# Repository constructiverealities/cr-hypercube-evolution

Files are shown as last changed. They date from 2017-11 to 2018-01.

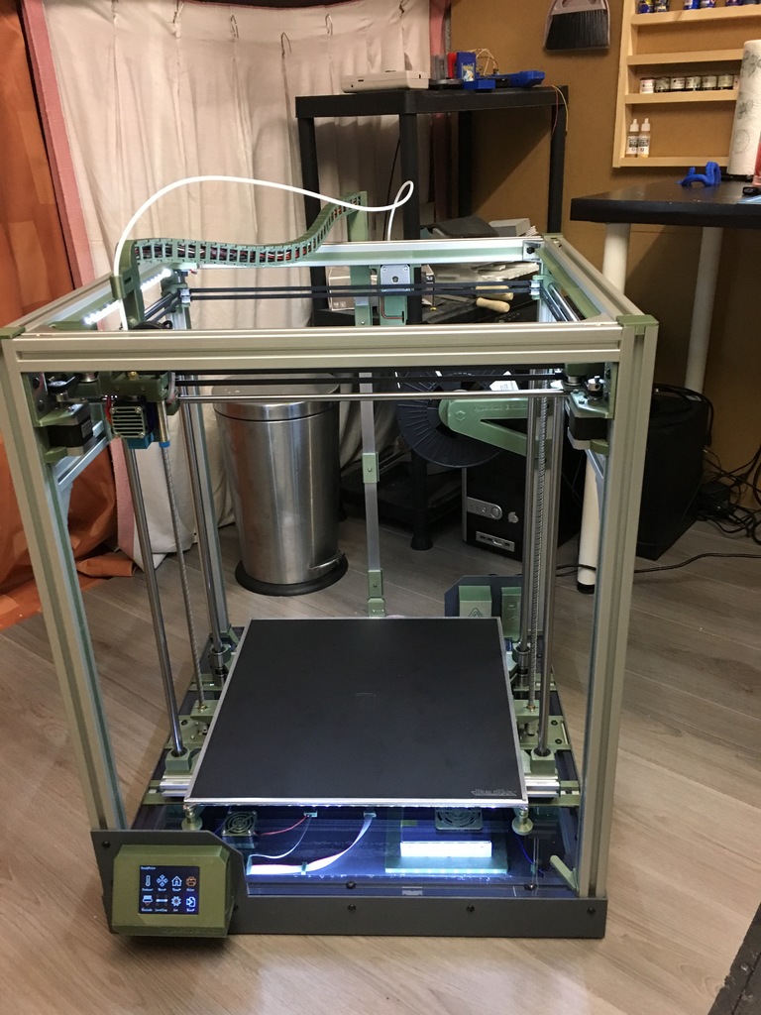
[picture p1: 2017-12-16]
hypercube photos/other/hypercube-build less-than 400.JPG

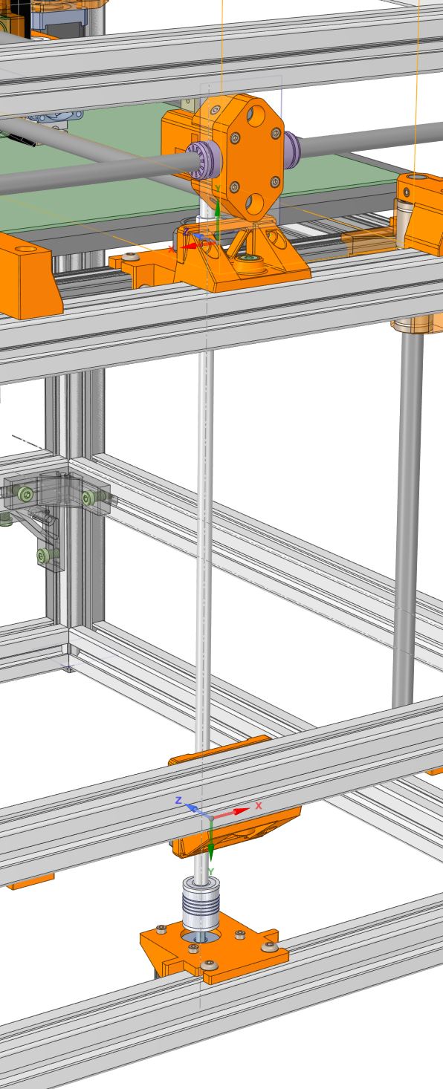
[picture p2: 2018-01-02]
hypercube photos/pillow-block-03.jpg

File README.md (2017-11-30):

# [Constructive Realities'](http://constructiverealities.io) Hypercube Evolution
---


## Introduction

This printer is used for our prototyping ad low volume production.  It's a third order derivative of the original hypercube designed by [Tech2C](https://www.thingiverse.com/Tech2C/about) and [SCOTT_3D](https://www.thingiverse.com/SCOTT_3D/about). and digitally housed here in this repository.  We've abandoned the single Z-platform version and only focus on the dual drive version.  

We've made some changes to the design and as part of our change control discipline keep track of those changes in this repository.  while the master branch of this repository should always contain a compatible set of design documents, you should rely on tagged versions for commits that are certain to have a coherent and compatible set of documents.

### Tools

This repository uses spaceclaim, so  design files are in their sdoc format.  In tagged commits you will that the latest completed assembly will exist in STEP format for that tagged release.  these will be more useful for you if you're a solidworks or (sic) Fusion360 user.

If you're looking for a power 3d design tool for viewing this machine, or to design for 3d printing, We recommend [DesignSpark mechanical].  If you're not familiar, It's a white label (limited/older) of SpaceClaim Engineer provided by rs-components.  It's a direct modeling tool with a legit geometry kernel (ACIS).  You'll need to register to "log in" to is, but It's a million times better then Sketchup for this type of (3d or mechanical) design.  

## Other Related Resources
- Original Hypercube on [Thingiverse](https://www.thingiverse.com/thing:1752766)
- Hypercube Evolution on [Thingiverse](https://www.thingiverse.com/thing:2254103)
- [hevo.wiki](https://hevo.wiki/index.php/Main_Page)

## Contributors

[Eric Schleicher](http://github.com/eric-schleicher)

## License

The original designs of this machine are CC-BY, which is a beautiful license for this type of thing.  We continue that here.

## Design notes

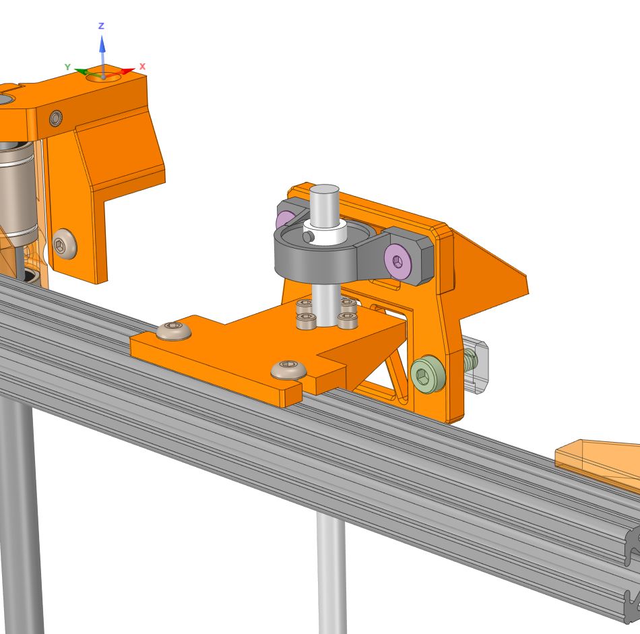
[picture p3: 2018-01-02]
hypercube photos/pillow-block-01.jpg

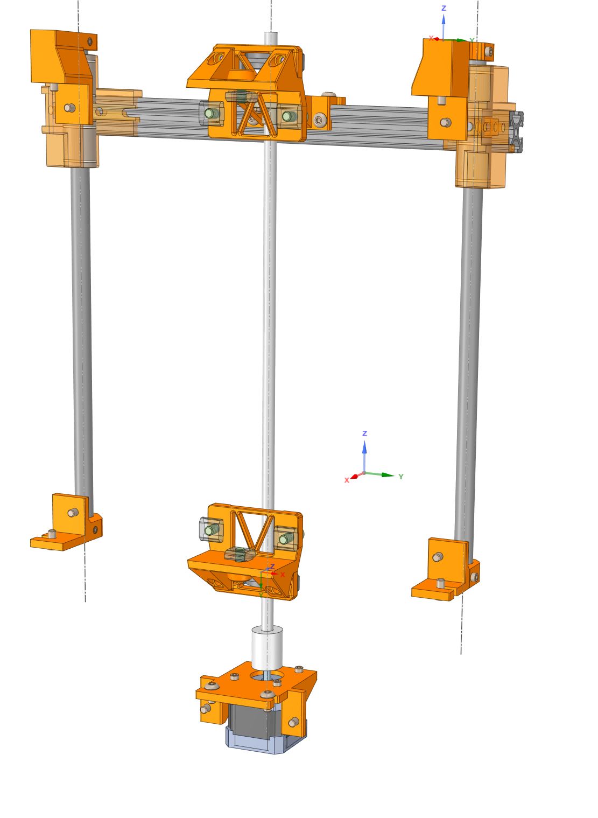
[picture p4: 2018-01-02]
hypercube photos/pillow-block-02.jpg

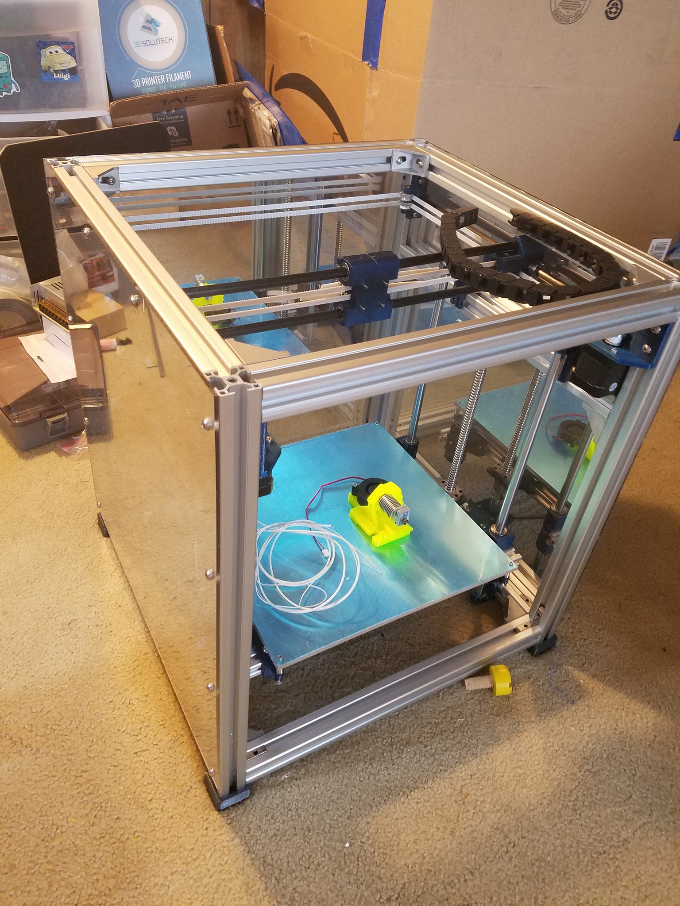
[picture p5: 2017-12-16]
hypercube photos/other/hypercube.jpg

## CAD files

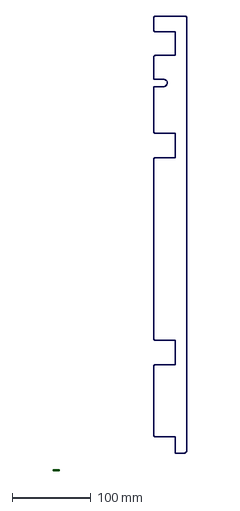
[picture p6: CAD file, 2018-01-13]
assembly-template-mm.dxf
169.9 x 577.9 mm

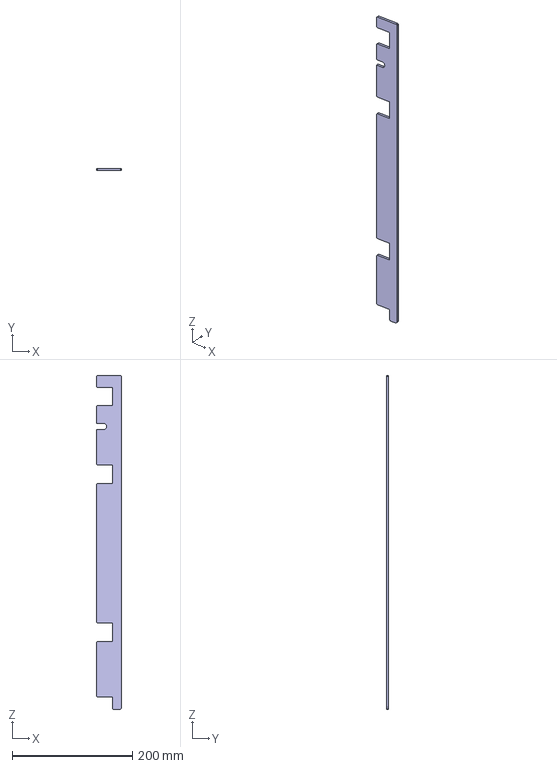
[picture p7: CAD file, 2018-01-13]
assembly-template.stp
42.0 x 4.13 x 555.7 mm

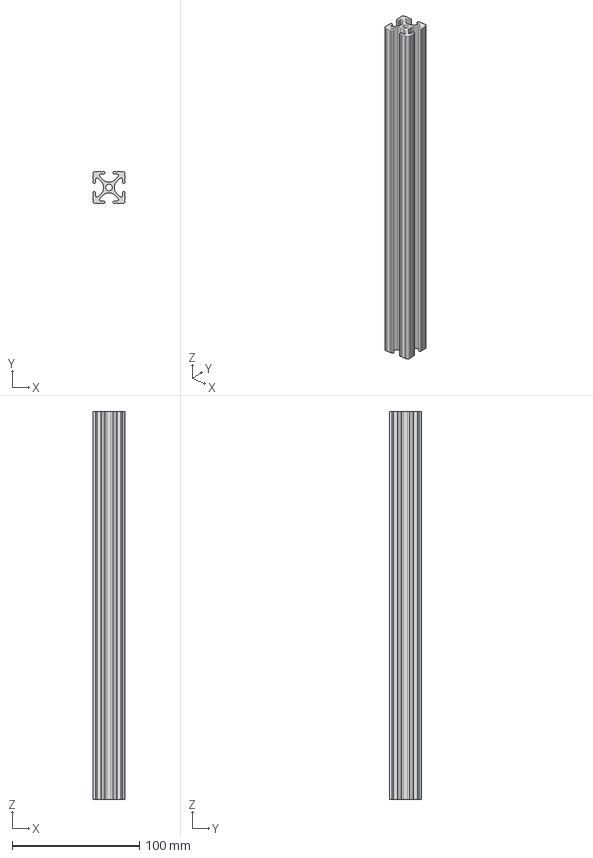
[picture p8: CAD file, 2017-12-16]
sources/8020/1010-12-CL.stp
25.4 x 25.4 x 304.8 mm

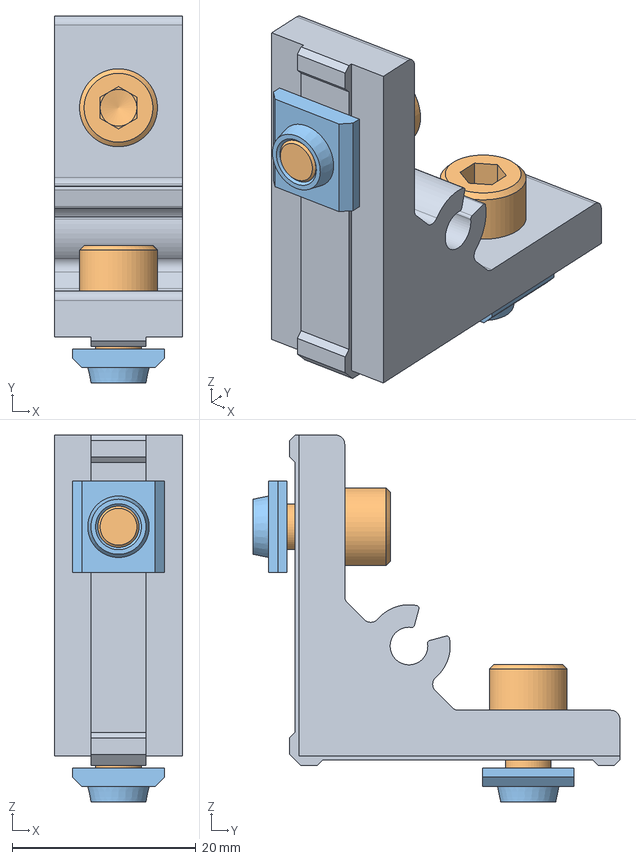
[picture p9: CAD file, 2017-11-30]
sources/mitsumi/source/HBKTST5-SST.stp
14.0 x 40.0 x 40.0 mm
_HBKTST5-SST_b
_SCB5-10_1 x 2
_HNTTBS5-5 x 2

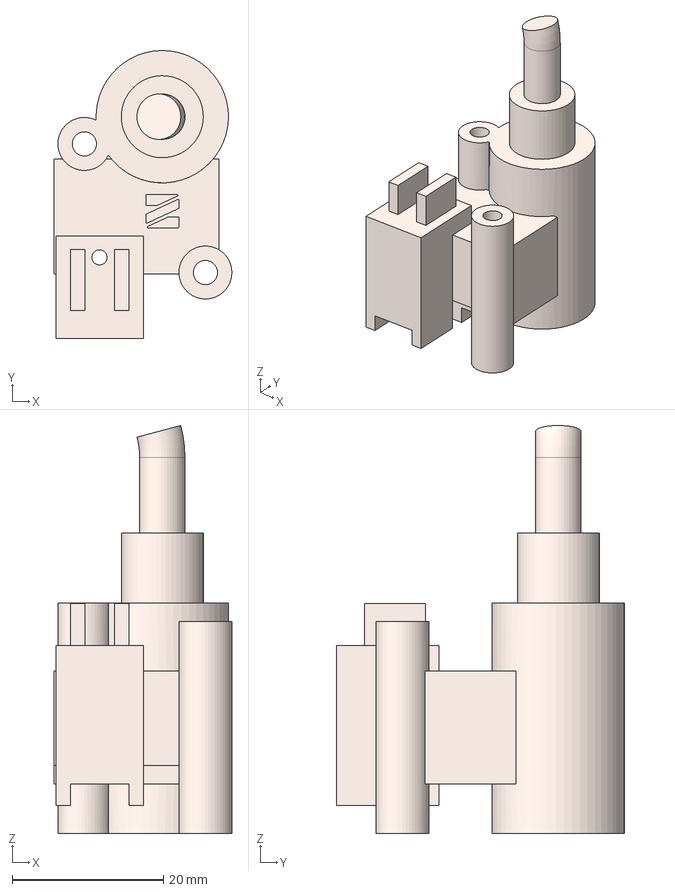
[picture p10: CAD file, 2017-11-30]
sources/nimble-extruder/source/Nimble_Mockup_right.stp
23.5 x 38.1 x 53.9 mm

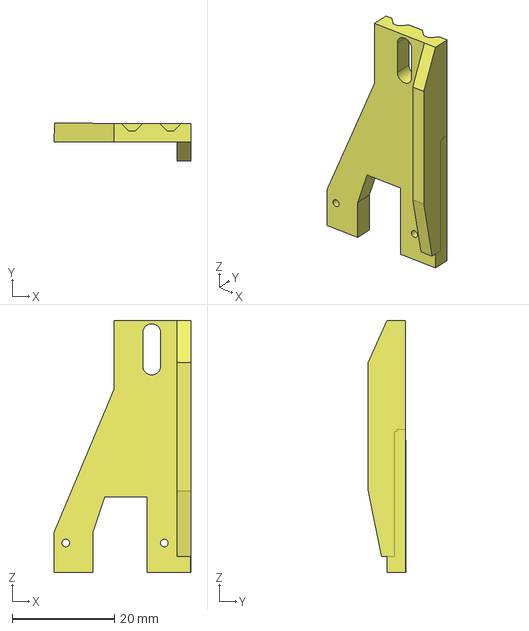
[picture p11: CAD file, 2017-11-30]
sources/nimble-hevo-mount/source/IR_sensor_mount.stp
26.7 x 7.36 x 49.3 mm

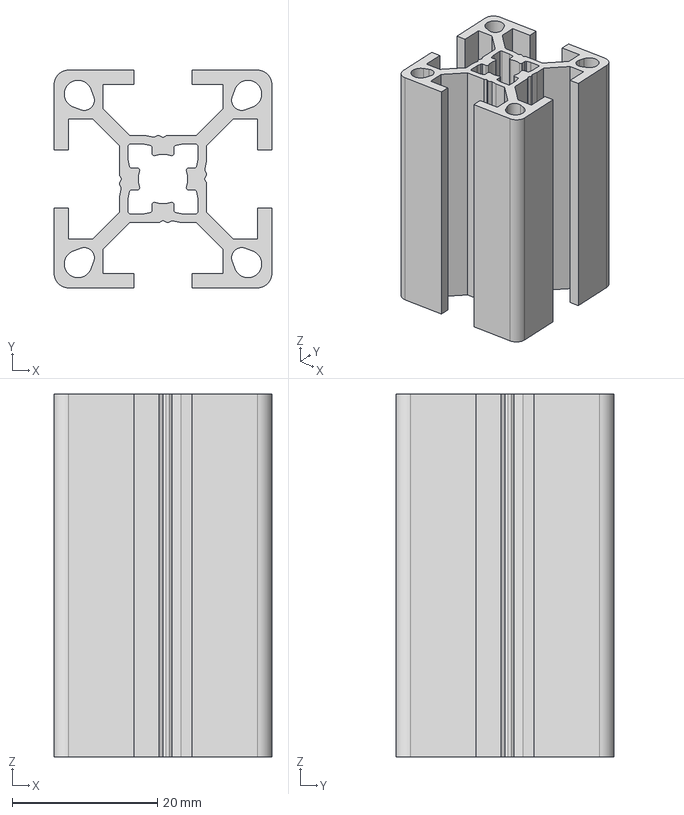
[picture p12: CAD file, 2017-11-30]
sources/mitsumi/source/NEFS6-3030-50.stp
30.0 x 30.0 x 50.0 mm

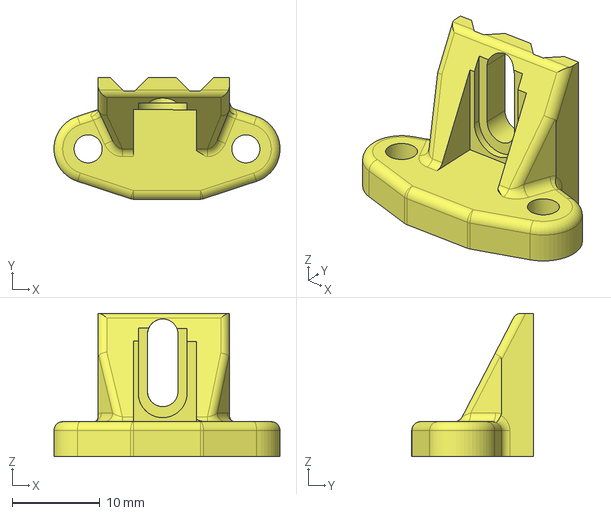
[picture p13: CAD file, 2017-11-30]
sources/nimble-hevo-mount/source/BLT_Mount.stp
25.8 x 13.9 x 16.4 mm

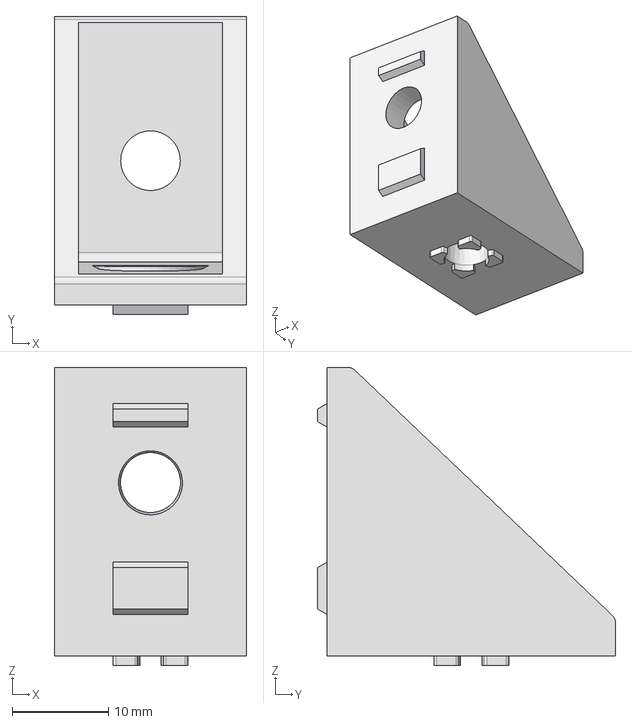
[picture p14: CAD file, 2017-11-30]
sources/mitsumi/source/HBLFSN6 [non-perpendicular].stp
20.0 x 31.0 x 31.0 mm

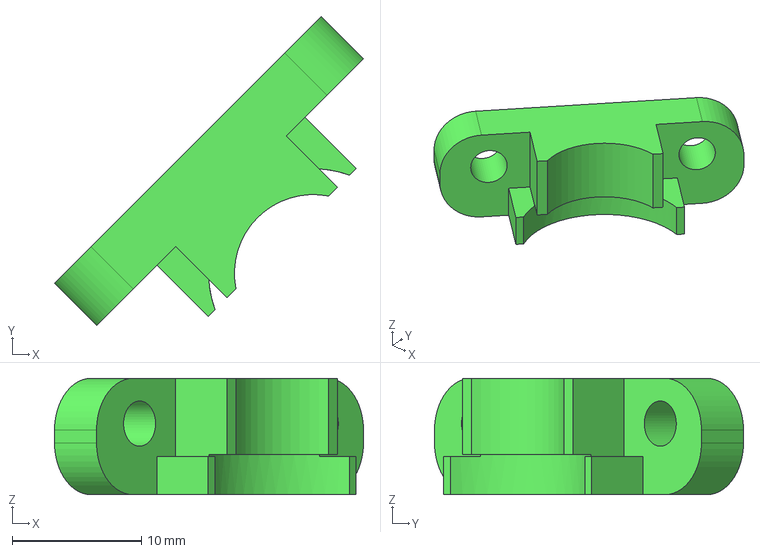
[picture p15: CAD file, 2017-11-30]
sources/nimble-hevo-mount/source/V6_Clamp.stp
23.9 x 23.9 x 9.00 mm

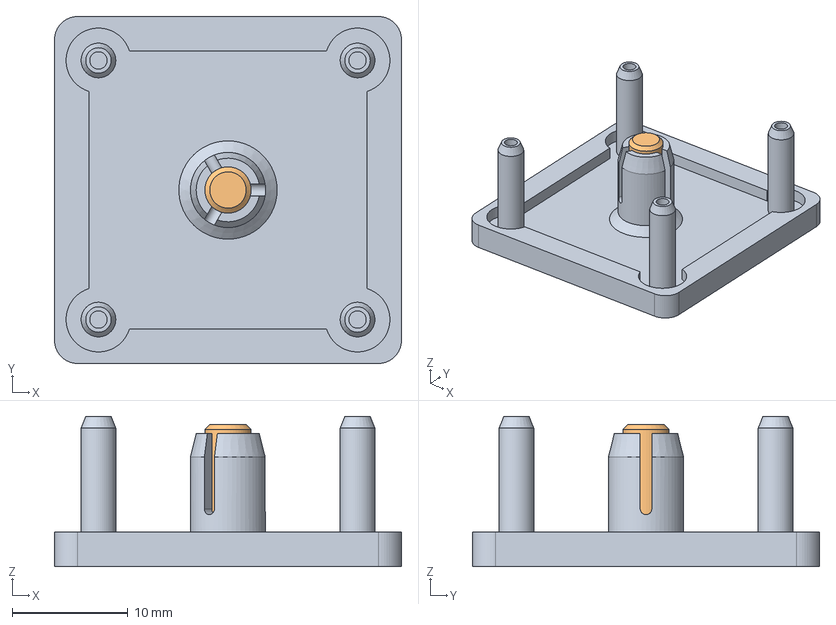
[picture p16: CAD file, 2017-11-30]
sources/mitsumi/source/HFCB6-3030-B.stp
30.0 x 30.0 x 13.0 mm
_HFCB6-3030-B_c
_HFBMB4-12

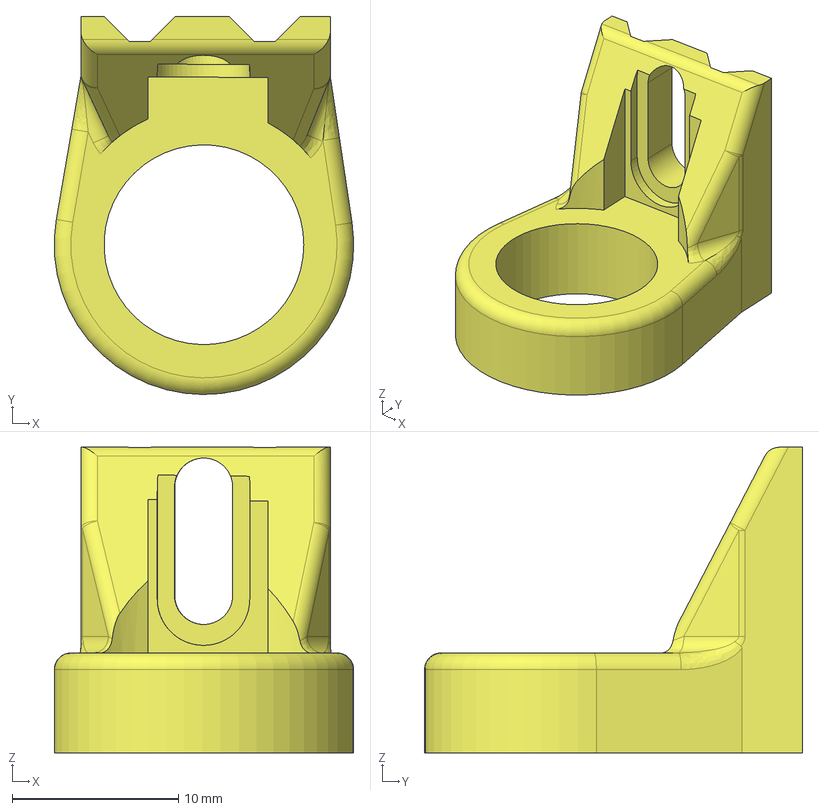
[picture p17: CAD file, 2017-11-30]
sources/nimble-hevo-mount/source/Induction_sensor_mount.stp
18.0 x 22.7 x 18.4 mm

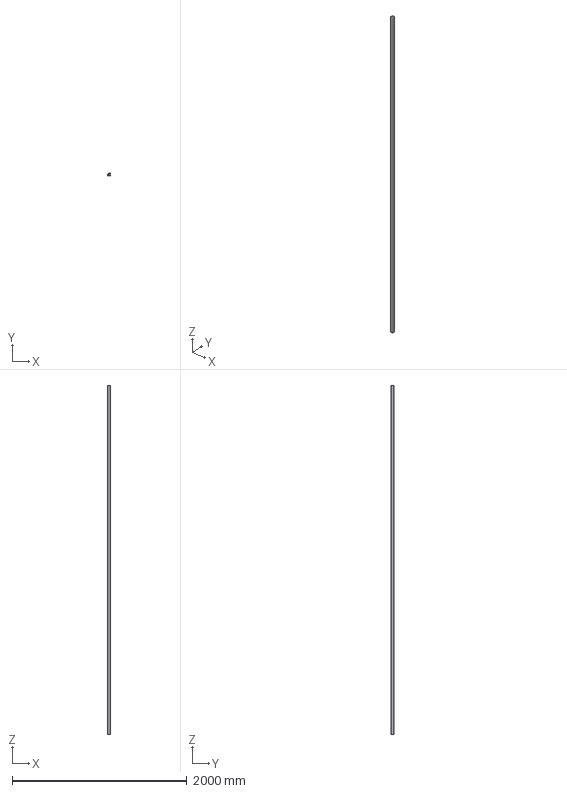
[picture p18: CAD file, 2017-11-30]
sources/mitsumi/source/KHFSR6-3030-4000.stp
30.0 x 30.0 x 4000.0 mm

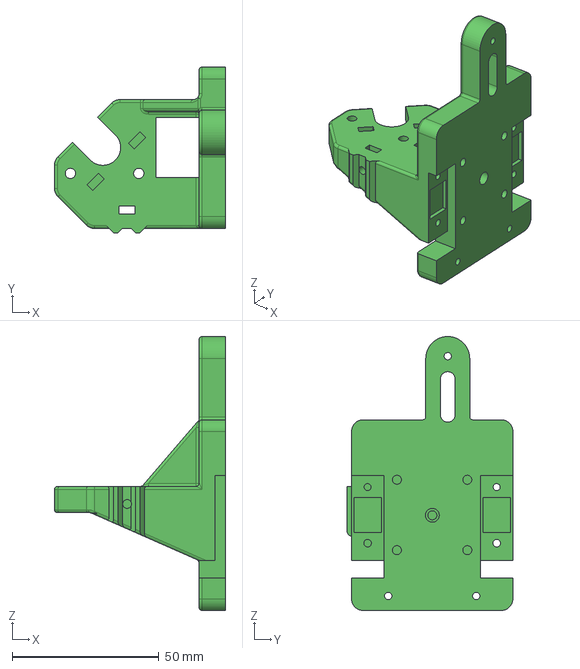
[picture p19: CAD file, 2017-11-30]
sources/nimble-hevo-mount/source/Basic_Mount_Single.stp
58.3 x 56.5 x 93.4 mm

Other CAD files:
sources/nimble-extruder/source/Nimble_Mockup_left.stp
sources/mitsumi/source/HBKTST6-SET.stp
sources/nimble-hevo-mount/source/DIY_sensor_mount.stp
sources/nimble-hevo-mount/source/Basic_Mount_Single_V1.1.stp
assembly-template.dxf
sources/mcmaster/source/12mm x 500 HARDENED PRECISION METRIC STEEL SHAFT [6112K520].STEP
sources/nimble-extruder/source/Nimble_Mockup_left.igs
sources/nimble-extruder/source/Nimble_Mockup_left.stl
sources/nimble-extruder/source/Nimble_Mockup_right.igs
sources/nimble-extruder/source/Nimble_Mockup_right.stl

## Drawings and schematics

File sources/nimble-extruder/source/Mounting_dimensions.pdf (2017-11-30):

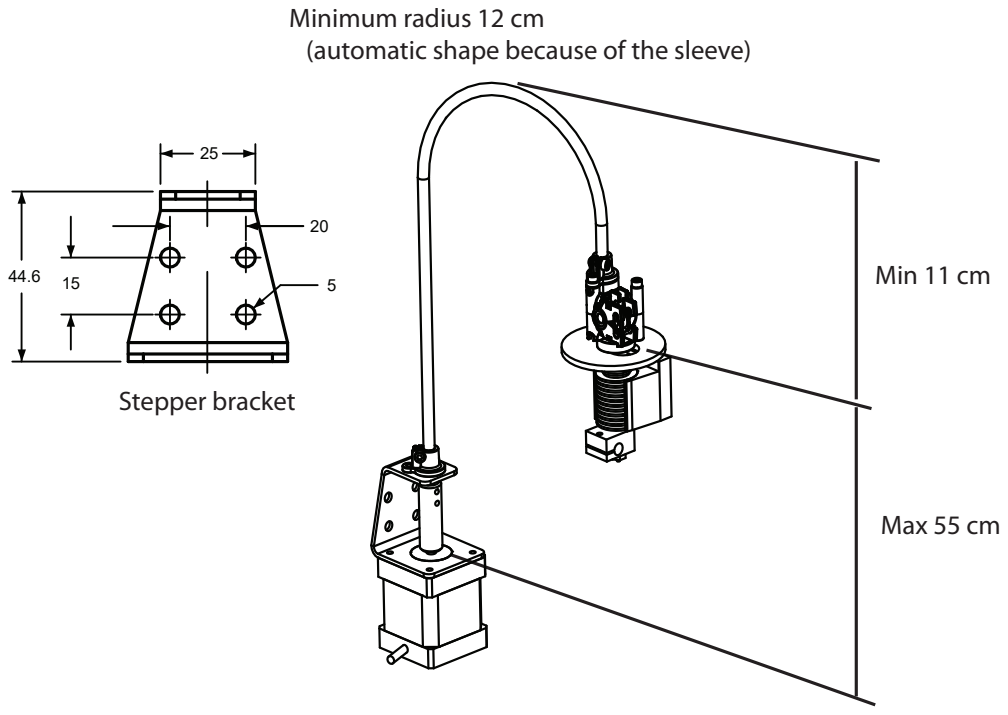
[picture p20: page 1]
Min 11 cm; Max 55 cm; Stepper bracket

Minimum radius 12 cm
(automatic shape because of the sleeve)

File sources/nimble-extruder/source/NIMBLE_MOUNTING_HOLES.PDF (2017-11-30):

2

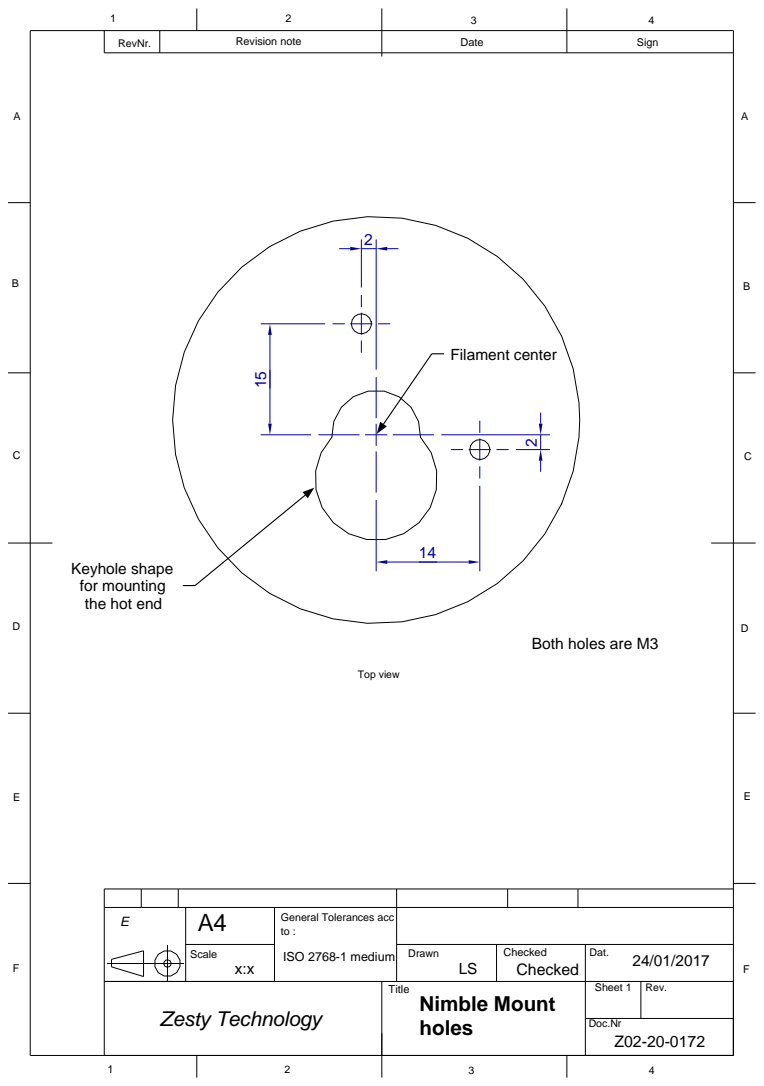
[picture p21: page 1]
Doc.Nr; RevNr.; Revision note; Date; Sign; Top view; Filament center

Keyhole shape
for mounting
the hot end

Both holes are M3

E | | General Tolerances acc A4 to : ISO 2768-1 medium

Scale | | Drawn LS | Checked | Dat. 24/01/2017
Zesty Technology | Title Nimble Mount holes | Sheet 1 | Rev.

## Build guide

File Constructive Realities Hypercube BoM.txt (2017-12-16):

Eric's Hypercube Frame BoM

#### Mitsumi Series 6 30 (18 parts total) 
- fore-aft (8) - 495mm
- laterals (6) - 500mm
- Uprights (4) - 545

#### Mitsumi Series ? 20 (4 parts total)
- lateral (2)  - 494mm
- fore/aft (2) - 300mm

[350x350 heated bed](https://www.aliexpress.com/item/Silicone-Heater-Bed-24V-350-X-350MM-For-Kossel-Pro-3D-Printer-Install-wih-100K-Thermistor/1982356777.html)

---
### Shafts: 
 - 10mm on Y Axis (2): 493.75  or 490 is acceptable margin.
  - [10mm shaft](https://www.ebay.com/itm/PDTech-10mm-dia-hardened-steel-linear-bearing-rod-chrome-custom-cut-USA-ship/252919812405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)
  
- 12 on Z Axis (4): 330 can be shortened.
  - [12mm shaft](https://www.ebay.com/itm/PDTech-12mm-dia-hardened-steel-linear-bearing-rod-chrome-custom-cut-USA-ship/252919837424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)

 - 10 mm on X; put ebay store info here 

Hardware: 

Carbon X Axis
[M3 x 20 Socket cap Screw] (https://www.boltdepot.com/Product-Details.aspx?product=13639)

 [*not* Oldham coupers :(](
https://www.zyltech.com/store/p87/Flexible_Plum_Coupling_Shaft_-_Various_combinations_from_5mm_to_12.7mm.html)

Damper
https://www.zyltech.com/store/p184/Nema_17_Dampers_-_refurbished_and_inspected_for_quality_-_3x%2C_4x%2C_or_5x.html

Acme assembly [400mm]
https://www.zyltech.com/store/p49/8mm_T8x8_Lead_Screw_Trapezoidal_ACME_w%2F_Anti-Backlash_Nut_kit_-_Pre-cut_lengths_150mm-2000mm.html

24v power supply
https://www.zyltech.com/store/p69/ZYLtech_24V_20A_480W_Power_Supply_Unit.html

optical end stops
https://www.zyltech.com/store/p105/3x_Optical_Endstop_Switch.html

m5x10
https://www.zyltech.com/store/p265/100x_ZYLtech_M5x8_and_M5x10_Button_Hex_Screws.html

24v fan
https://www.amazon.com/gp/product/B016XMK6SE/ref=ox_sc_act_title_3?smid=ATVPDKIKX0DER&psc=1

14 gauge silicone wire
https://www.amazon.com/gp/product/B074MGBMGX/ref=ox_sc_act_title_2?smid=A1AY59LT54ZBYI&psc=1

brass inserts
https://www.amazon.com/gp/product/B01IYWUUH8/ref=ox_sc_act_title_1?smid=A1THAZDOWP300U&psc=1

gt2 belt
https://www.amazon.com/gp/product/B00YMM6IQW/ref=ox_sc_act_title_4?smid=A2UHE58S2974CT&psc=1

20 tooth gt2 wheels
https://www.amazon.com/gp/product/B01H3DSGAC/ref=ox_sc_act_title_5?smid=A1LCDIR1SM8KTJ&psc=1

leveling screws
https://www.amazon.com/gp/product/B0761TLRNY/ref=ox_sc_act_title_6?smid=A2QQQKMKGVNA5E&psc=1

pins
https://www.amazon.com/gp/product/B01DZZUD3A/ref=ox_sc_act_title_7?smid=A1THAZDOWP300U&psc=1

hidden corner brackets
https://www.ebay.com/itm/172679113288

t5 drop in t-nuts for 3030 
https://www.ebay.com/itm/122537947289

Mitsumi 
-----------------------------
16 x HBKTST6 - https://us.misumi-ec.com/vona2/detail/110302061170?ProductCode=HBKTST6
2 x PSFJ10-490 - https://us.misumi-ec.com/vona2/detail/110302634310?ProductCode=PSFJ10-490
4 x PSFJ12-400 - https://us.misumi-ec.com/vona2/detail/110302634310?ProductCode=PSFJ12-400
4 x HFS6-3030-545 - https://us.misumi-ec.com/vona2/detail/110302686450?ProductCode=HFS6-3030-545
2 x HFSR6-3030-545 - https://us.misumi-ec.com/vona2/detail/110302688550?ProductCode=HFSR6-3030-545
6 x HFS6-3030-500 - https://us.misumi-ec.com/vona2/detail/110302686450?ProductCode=HFS6-3030-500
8 x HFS6-3030-495 - https://us.misumi-ec.com/vona2/detail/110302686450?ProductCode=HFS6-3030-495

Bearings

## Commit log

2017-11-30 Initial commit of the Hypercube Evolution in Spaceclaim format.
    [12mm x 500 HARDENED PRECISION METRIC STEEL SHAFT [6112K520].STEP, BLT_Mount.stp, Basic_Mount_Single.stp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]
2017-12-08 pulled in 8020 1010 series extrusion and started looking at breaking out the component with a new (sane) naming convention
    [1010-12-CL.stp]
2017-12-16 Added two pictures and update some BOM info
2017-12-16 added new hidden inside corner-bracket file
2017-12-17 Changes to the inside corner bracket
2017-12-17 Revisions to end caps (these will be printed)
2017-12-17 Modifications to x shuttle for printing.
2017-12-20 Remove gt2 pulley files (in favor of versions with stated size)
2017-12-20 Added two new gt2 pulleys and added integration folder exclusion to .gitignore
2017-12-20 Catch up to current state. recently modified the XY idler end stops to make then a bit stronger and to use 3d-printed threads were it makes sense.
2018-01-02 Resolved design for the z axis pillow blocks.
2018-01-02 Revision to complete the z pillow block mount (made holes in it).
2018-01-10 Updated de-metricify the main platform - urg :(
2018-01-13 added template for assembly
    [assembly-template.dxf, assembly-template.stp]
2018-01-13 adding mm version of template
    [assembly-template-mm.dxf]
2018-01-16 update of the assembly template
